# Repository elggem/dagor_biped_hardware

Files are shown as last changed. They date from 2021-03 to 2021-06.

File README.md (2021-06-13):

# dagor_biped_hardware

<p align="center">
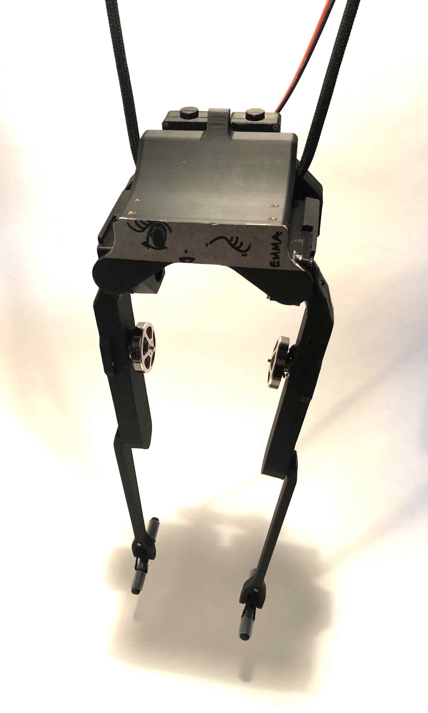
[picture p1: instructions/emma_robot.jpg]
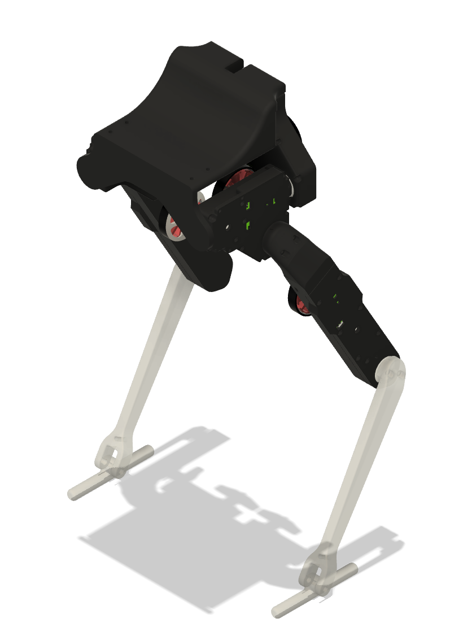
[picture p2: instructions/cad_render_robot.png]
    
</p>

This is a robot hardware design based on the the [Open Robot Dynamic Initiative](https://github.com/open-dynamic-robot-initiative/open_robot_actuator_hardware) Bolt robot remixed for easier and cheaper assembly using commonly available FDM 3D printers and control via the [Dagor Brushless motor control module](https://www.dagor.dev). The following modifications were made to the original design:

  - The body and cover of the actuator modules are modified to make them print easily without supports on an entry level FDM printer in ASA/PLA.
  - Change of belt to 3M HTD profile. This curved belt profile might not be ideal in terms of backlash and other performance characteristics, but it is more affordable than the AT3 GENIII Conti belts used in the original ODRI work. Other (trapezoidal) tooth profiles might be better suited for this application.
  - Change of gear ratio from 1:9 to 1:8. This leads to slightly less torque but also faster speed. The change was made to accomodate a bigger transmission pulley with 12/32 instead of 10/30 teeth, which allows printing the pulley on an FDM printer in PLA.
  - Change to 4004 360kV budget motors. Change to mounting holes and design of custom Hex-based motor pulley to avoid having to make a custom motor shaft.
  - Mounting holes for [Dagor Brushless Controller module](https://www.dagor.dev). 

## Instructions

### Motor pulley
<p align="center">
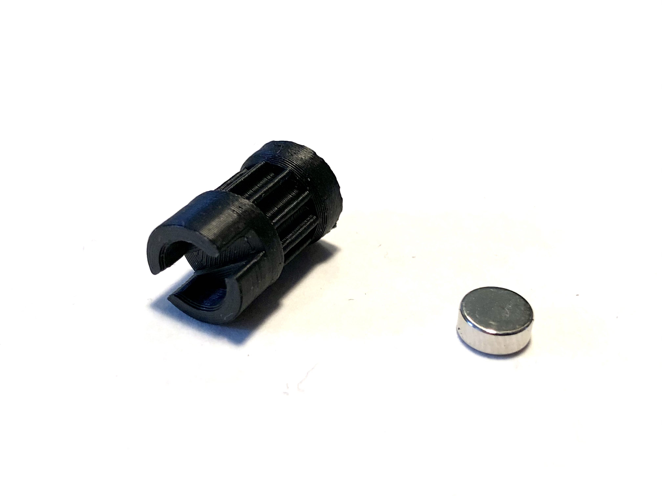
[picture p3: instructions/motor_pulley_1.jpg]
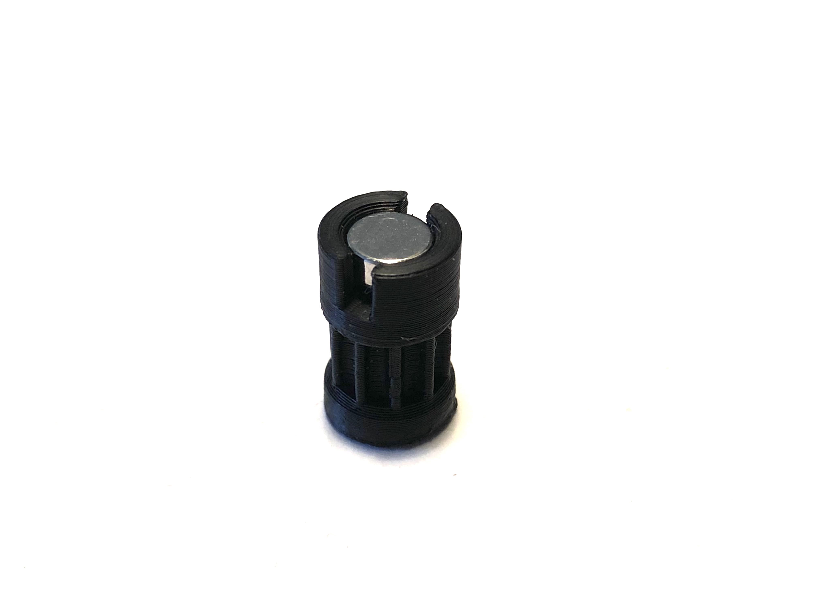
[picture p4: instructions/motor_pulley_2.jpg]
  
</p>

The motor pulley press-fits onto the brass or steel standoffs on the finished motor assembly. This pulley has to be printed using SLA with resin, it is too small to be printed using an FDM printer in my experience.

### Output pulley
<p align="center">
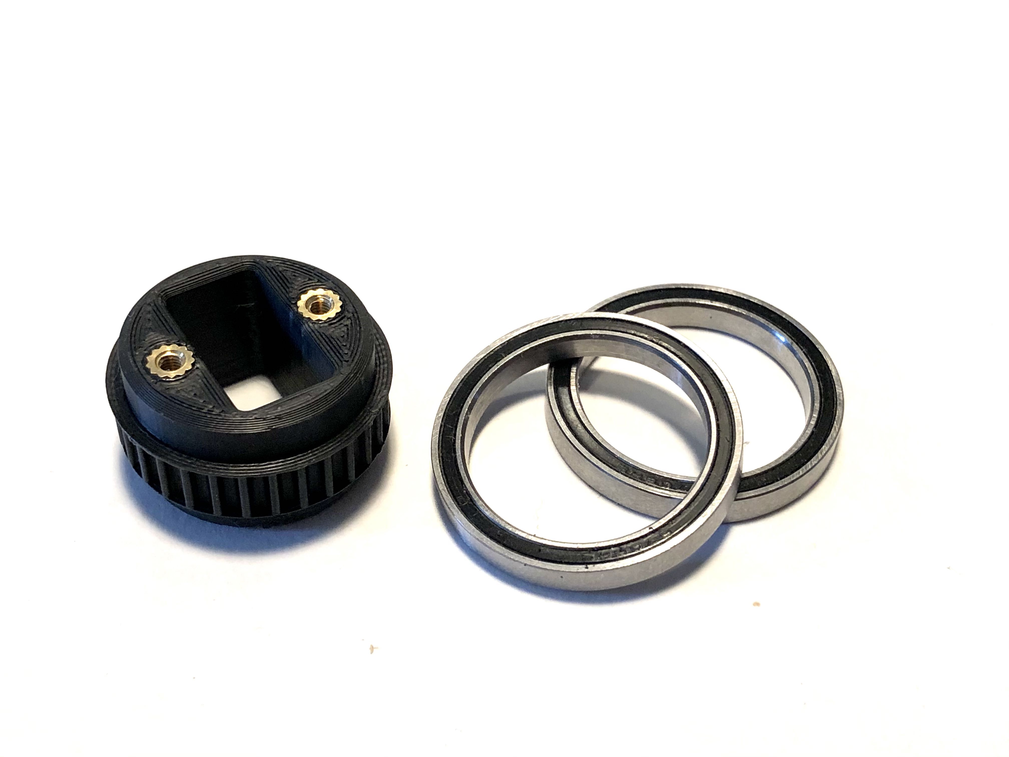
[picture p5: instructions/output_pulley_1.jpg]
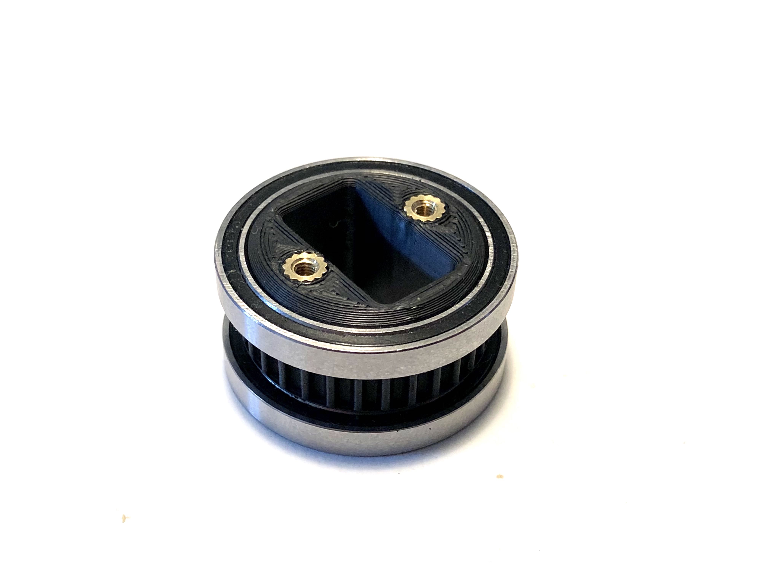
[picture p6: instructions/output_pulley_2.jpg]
  
</p>

Two threaded inserts are placed on the output pulley and two 6705 bearings attached.

### Center pulley

<p align="center">
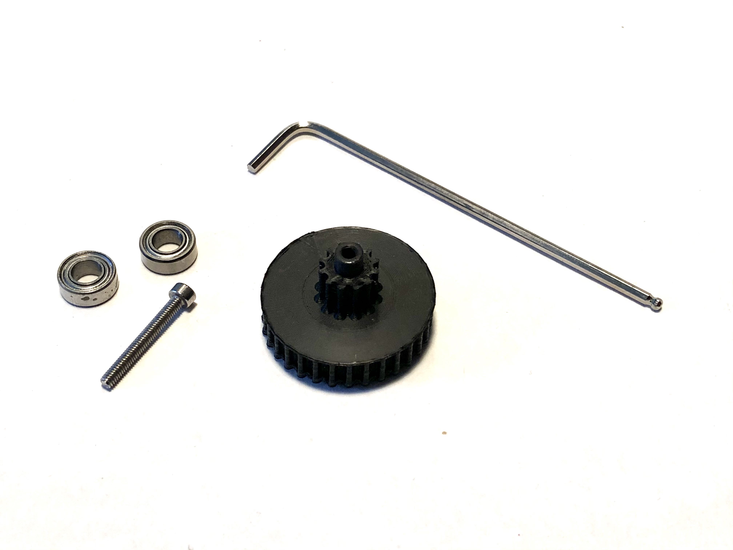
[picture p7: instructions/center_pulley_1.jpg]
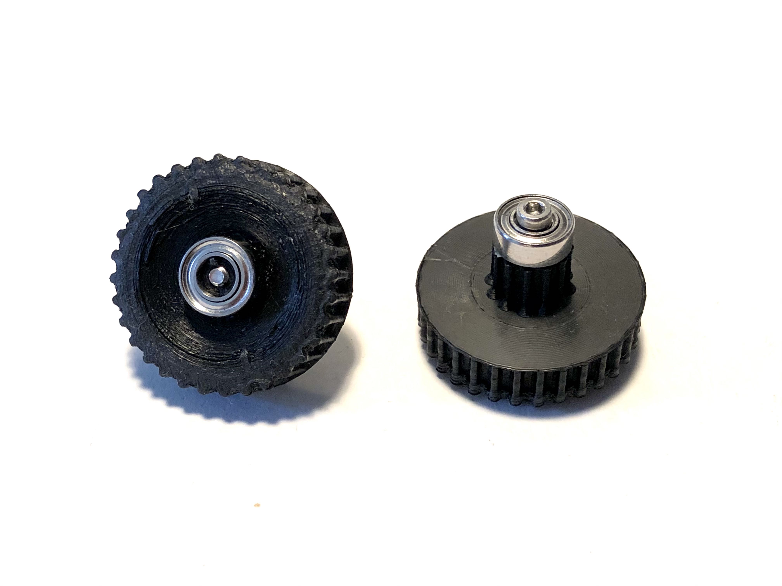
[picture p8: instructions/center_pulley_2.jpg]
  
</p>

The center transmission pulley is under a lot of stress and needs to be fabricated as strong as possible. In many other designs this pulley is machined from aluminium using CNC to avoid breaking it. It would also make sense to print it out of a strong material such as Nylon or Polycarbonate. To make this piece out of PLA, a few custom slicer settings need to be made for extra strength.

1. We printed the pulley with the maximum resolution of 0.08mm on an Ender 3 in PLA. This enables the underside of the pulley to print without supports.
2. Part cooling needs to be turned off during print except for the very top circular shape that connects to the bearing. In our case we turned on part cooling at layer 192. No part cooling increases layer adhesion significantly and is absolutely recommended. To make this work with enough precision we decreased the output perimeter speed to 5mm/s. 
3. The extrusion width needs to be optimized to avoid gaps between the tooth profile and inner body of the pulley. In our case the optimal extrusion width was 0.3mm for inner and outer perimeters.
4. We set the perimeter count to 32 so that the pulley prints entirely as perimeters with no infill. This maximizes the contact area between the bigger bottom pulley and smaller top pulley.
5. We set the extrusion multiplier to 105% to increase layer bonding even further.

After printing, a 20mm M2.5 bolt is screwed into the pulley to further strengthen it from top to bottom. Then the MR105 bearings can be press-fit into place.

### Preparing the motor shaft

<p align="center">
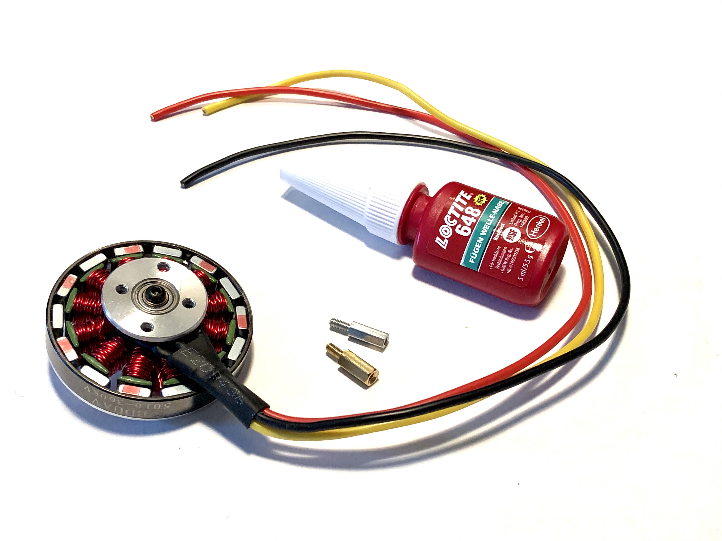
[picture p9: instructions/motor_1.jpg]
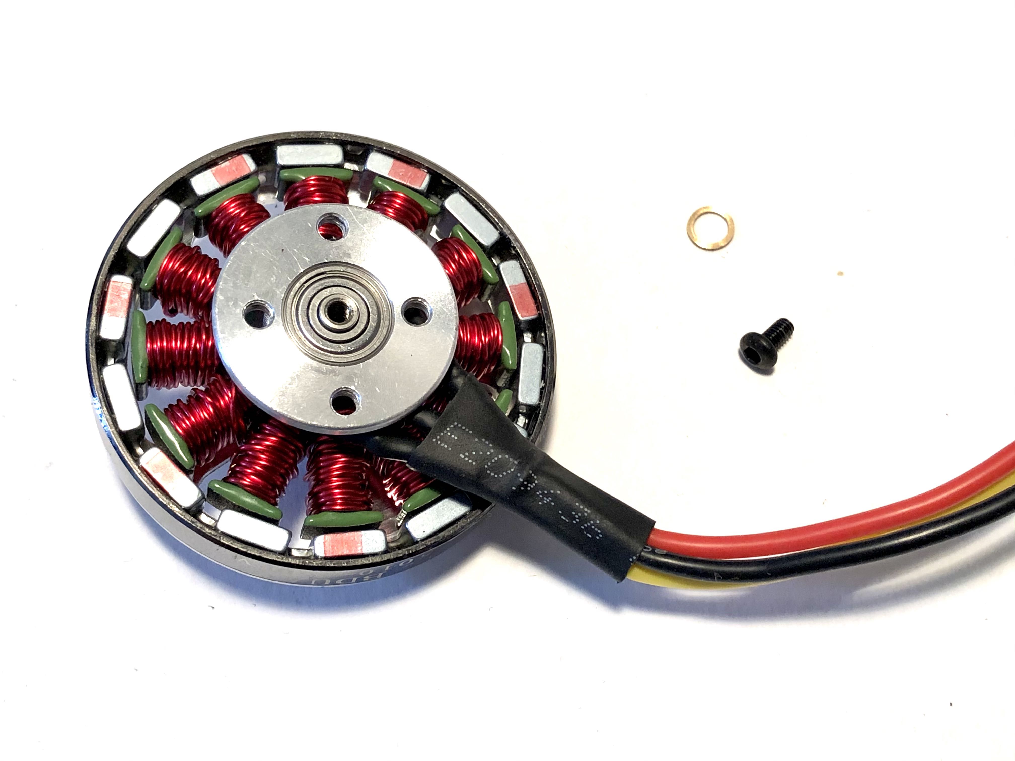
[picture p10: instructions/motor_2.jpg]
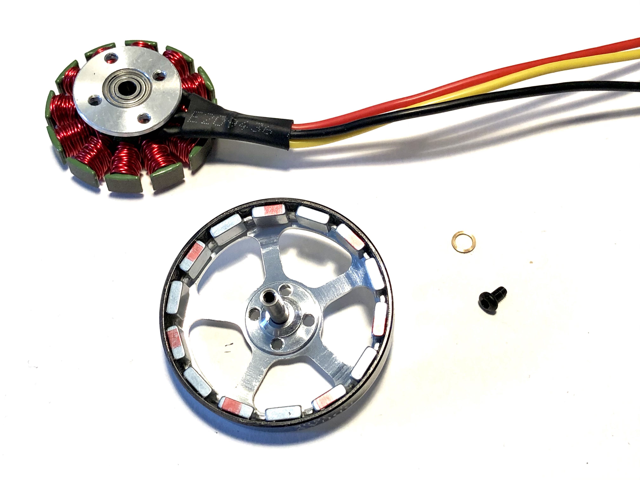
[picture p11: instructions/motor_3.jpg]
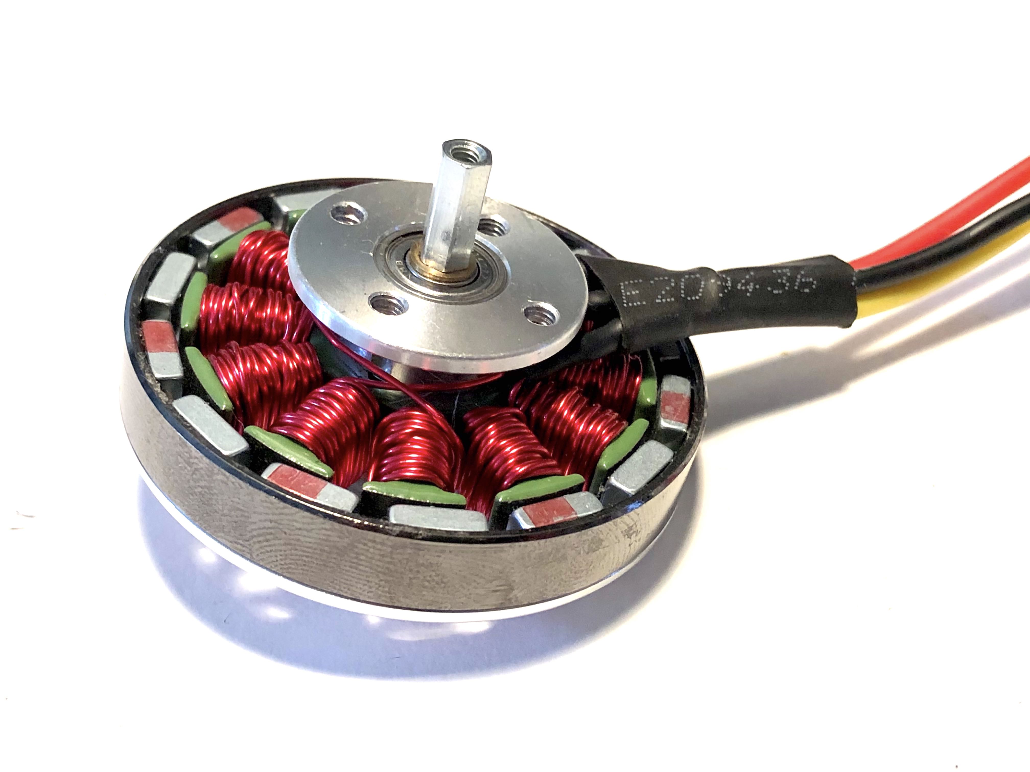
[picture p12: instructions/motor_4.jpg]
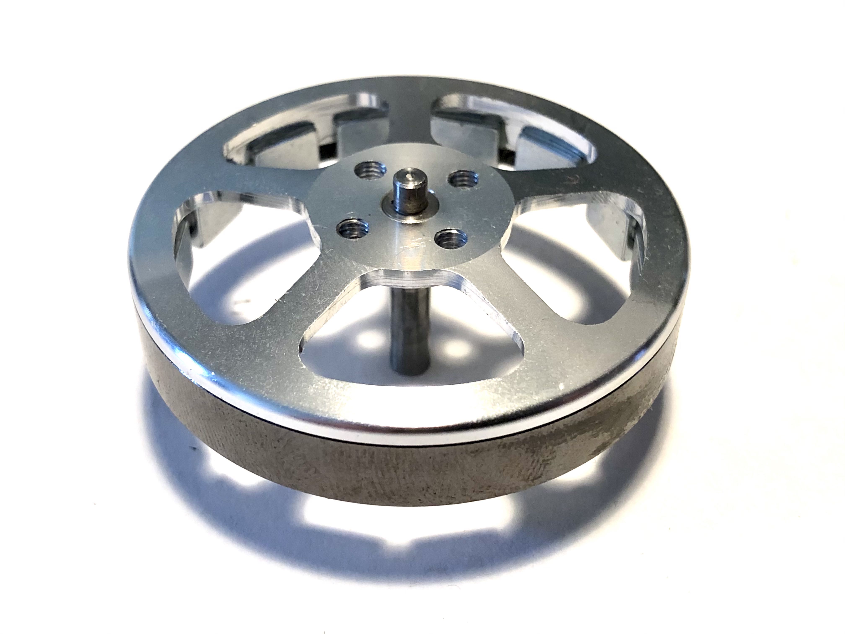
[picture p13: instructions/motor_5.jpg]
  
</p>

There are M2.5 threads on the output shaft of the Sunnysky motors we used in this build. If you use other motors or receive another batch of these motors without the thread then you have to find another way of mounting the output transmission pulley onto your motors. This might involve replacing the shaft of the motor entirely (for examples see [here](https://github.com/open-dynamic-robot-initiative/open_robot_actuator_hardware/blob/master/mechanics/actuator_module_v1/details/details_motor_shaft_preparation.md) and [here](https://youtu.be/HwWZw7wfN_k?t=182)). In our case, the process is quite simple:

 1. Remove the original M2.5 lockscrew on the output shaft of the motor and seperate the outer case from the stator. Due to the magnetic force this requires quite a bit of strength. Be aware not to pinch your fingers.
 2. Use a hard flat surface to push the output shaft from the outer case a little bit. Apply Loctite 648 or another suitable anaerobic metal glue onto the surfaces and push the shaft back into the housing. Remove any residual glue that was squeezed out from the outside.
 3. Snap the stator back into the housing carefully. After apply some Loctite 648 to the M2.5 standoff and screw it into the shaft as tight as possible with pliers. We use steel standoffs here, but the more commonly available brass standoffs would probably also work.
 4. Wait for the Loctite to cure at least 24hr. Then slide the 3D printed motor output pulley over the standoff. It should be a very tight press-fit between the pulley and standoff.
 5. Finally insert the magnet used for the magnetic encoder into place. It should also be a pretty tight fit. If it falls out very easily apply a little amount of glue to fix it in place.

### Preparing Dagor boards

<p align="center">
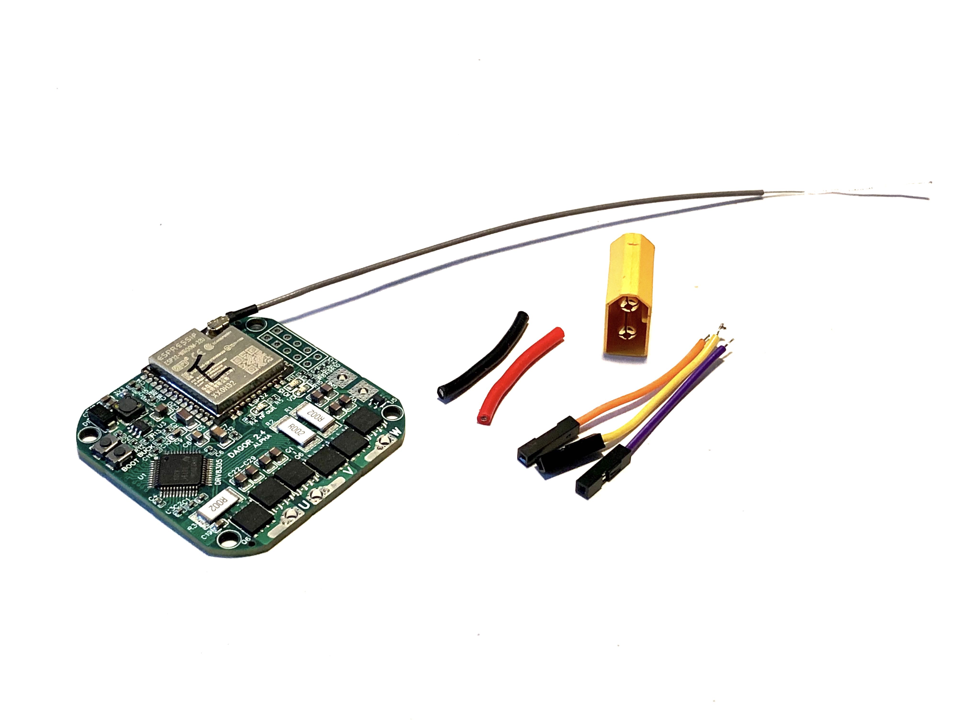
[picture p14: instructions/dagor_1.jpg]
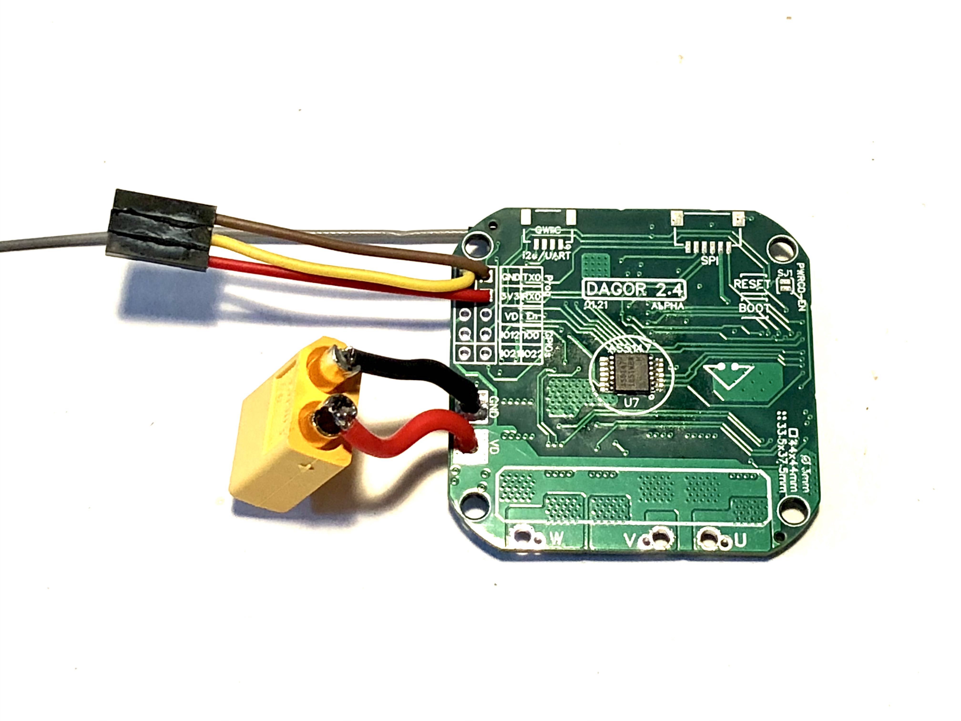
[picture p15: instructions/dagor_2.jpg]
  
</p>

 1. Prepare a 3-pin female programming header connection cable with ~4cm length and put some solder on the exposed leads. Solder the programming wires on to RXD/TXD/GND on the Dagor board, with the leads exiting the PCB towards the side with the magnetic encoder. 
 2.  Prepare an XT60 male connector with ~2cm leads for the hip modules and a ~15cm power wire without a connector for the leg modules. Solder the power wires on the side of the module with the magnetic encoder.
 3. Optionally you could use bullet style connectors for the motor wires, but I choose to solder them onto the board directly after assembly. If you want to also solder directly just put some tin onto the pads of the controller. The leg modules have enough space for connectors but in the hip modules its a very tight fit.

### Actuator assembly

<p align="center">
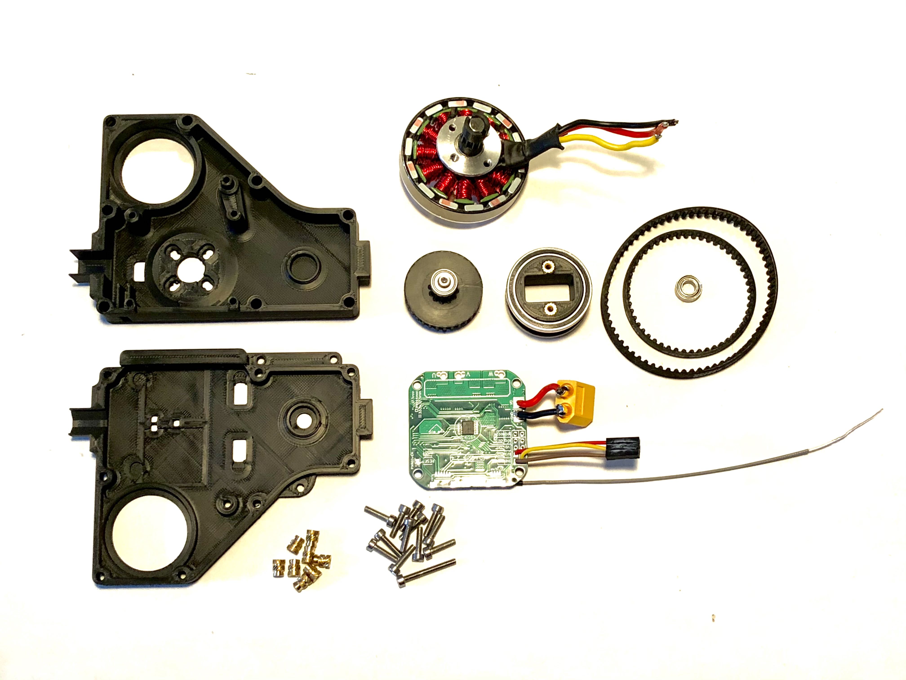
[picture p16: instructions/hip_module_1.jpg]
  
</p>
<p align="center">
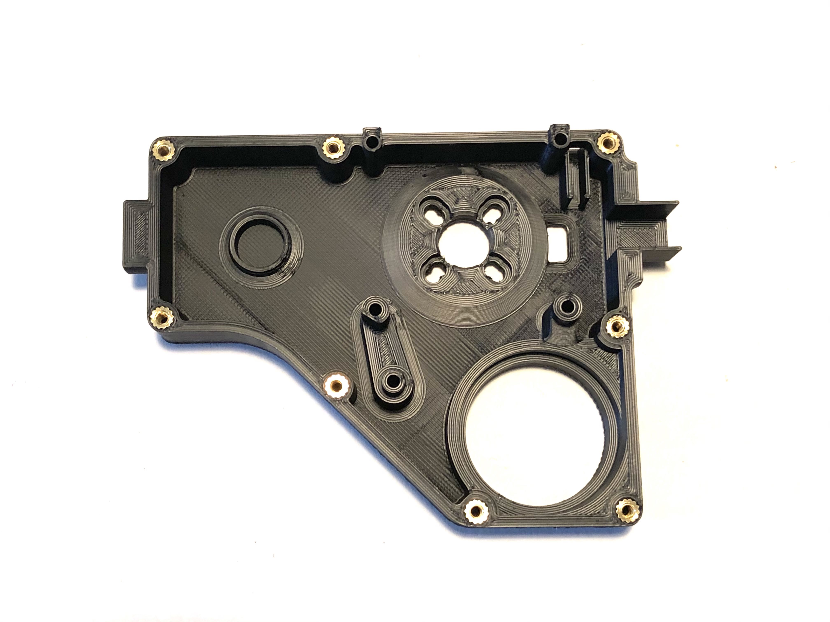
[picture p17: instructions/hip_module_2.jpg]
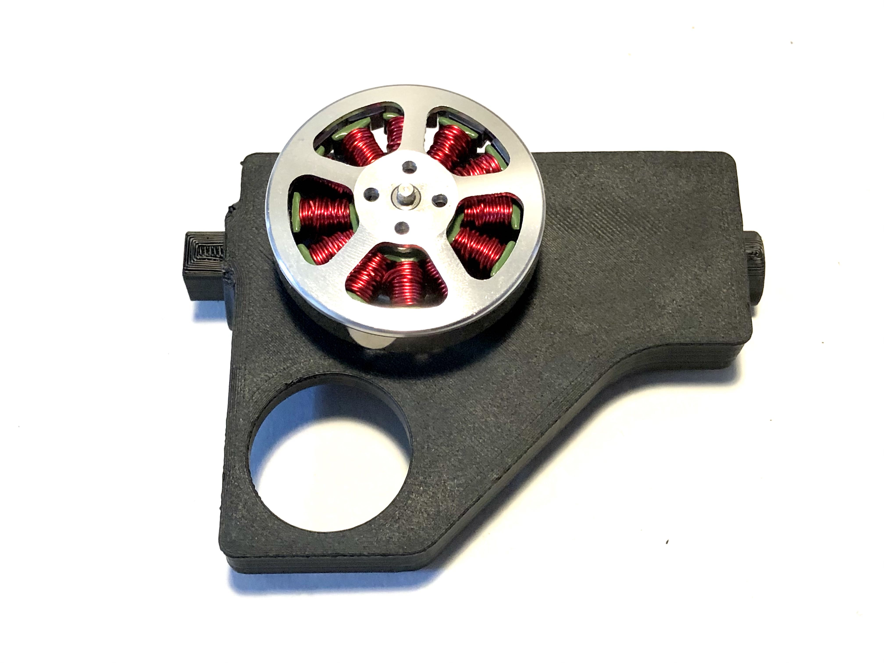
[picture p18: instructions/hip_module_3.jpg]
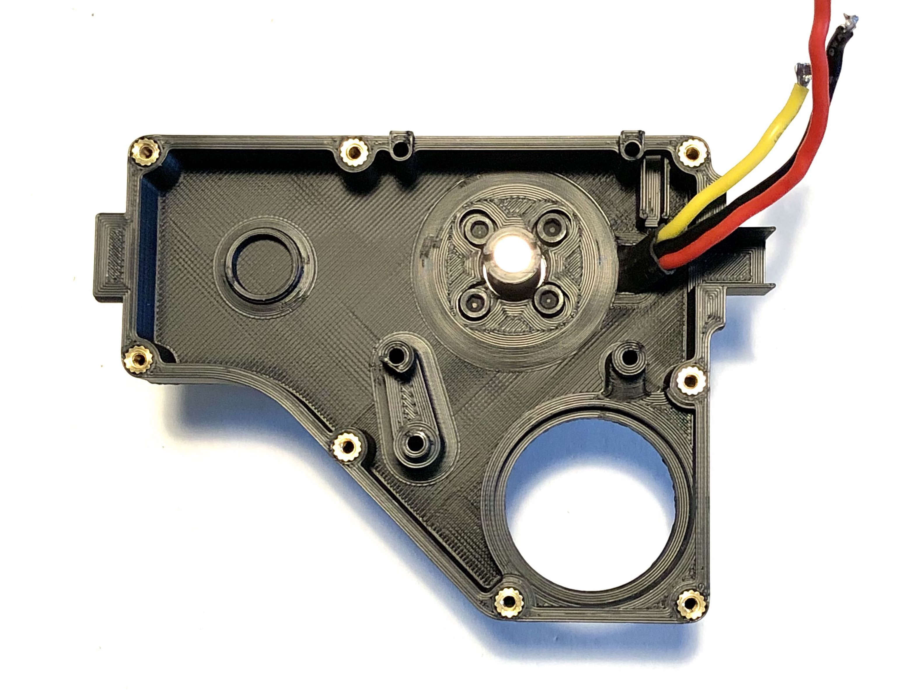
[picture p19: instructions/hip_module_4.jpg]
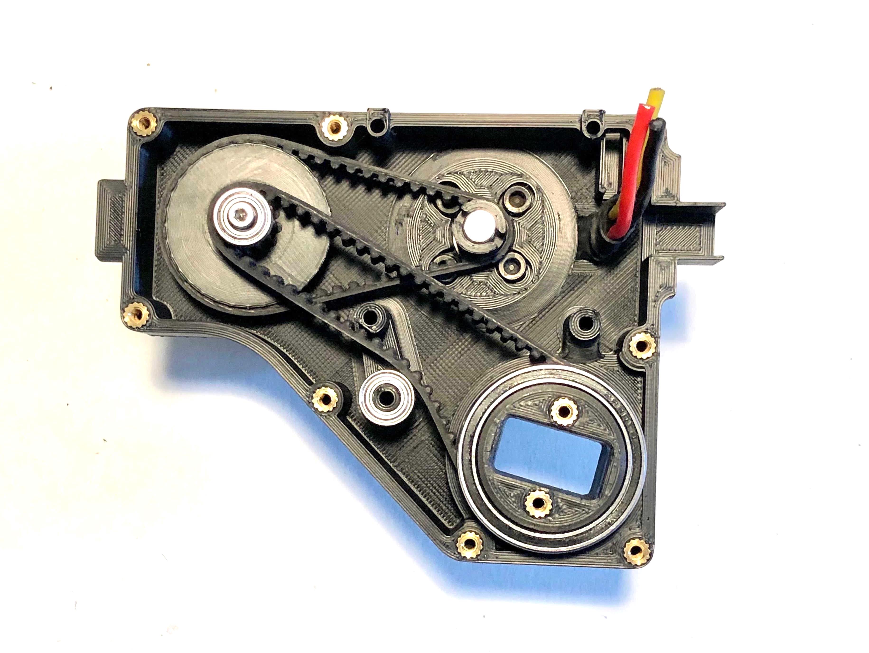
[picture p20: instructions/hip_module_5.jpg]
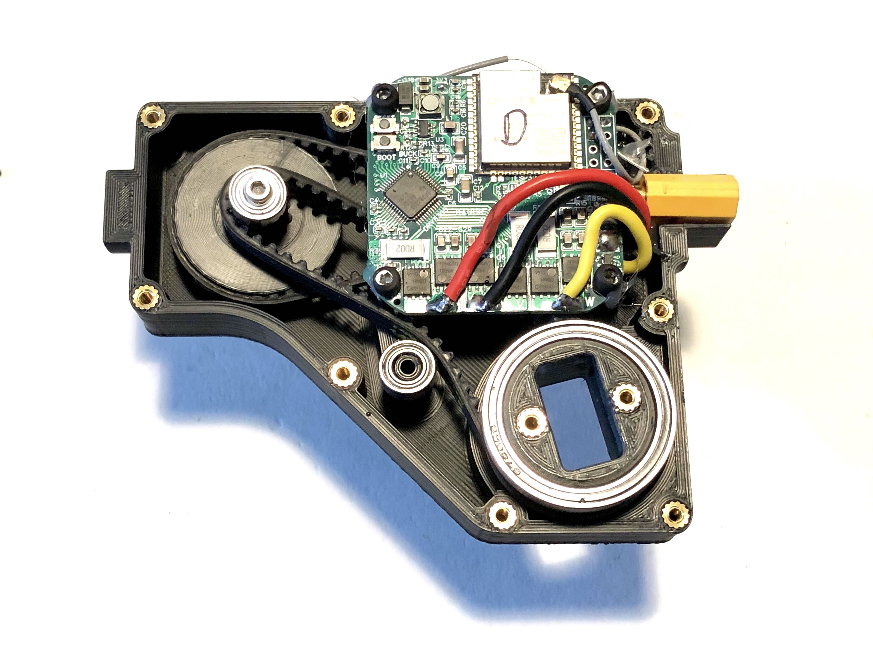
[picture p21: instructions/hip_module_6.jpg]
  
</p>

*Final weight of hip module: 188g*

Make sure that both the smaller MR105 and bigger 6705 bearings press fit tightly in their places!

1. Use a soldering iron to place 8x threaded inserts into the provided holes on the body of the actuator module.
2. Mount the finished motor assembly onto the body of the actuator module, feeding the wires through the hole. Dont worry about the length of the motor cables at this point.
3. Take the assembled transmission pulley and press it into the mounting hole while adding the 50 tooth belt between the motor and transmission pulleys. There will be some tension here and the transmission pulley will be slightly slanted towards the motor. That is ok. You can keep tension on the transmission pulley and give the motor a few turns to see if it is spinning freely.
4. Press fit an MR105 bearing onto the belt tensioning post in the body of the module. Make sure it sits flush with the bottom and be sure not to apply too much force to the post. It will be strengthened by a bolt in the final stage of assembly.
5. Place the output pulley assembly into its hole on the body while adding the 67 tooth belt between it and the transmission pulley. Quickly give the motor a few turns while keeping pressure on the transmission pulley to make sure the output pulley turns. Dont apply too much force to avoid breaking the belt tensioning post.
7. Place a Dagor board onto the mounting posts and screw in 4x M2.5 bolts to secure it.
8. Place the programming and power connectors into their sockets and glue them into place with either hotglue or superglue.
9. Shorten and solder the motor wires onto the Dagor board. Optionally you can use bullet style connectors for this.
10. Place the cover on top of the base. You need to slip it over one side of the Dagor board and wiggle both the transmission and output pulleys into place to make it work. The belt tension will make this a bit tricky, be patient and dont apply too much force.
11. Screw the 8x M2.5 10mm bolts into place securing everything.
12. Finally, screw one M2.5 20mm bolt into the hole of the belt tensioner. This is essential because otherwise the belt tensioning post will break off.
13. Check that everything runs smoothly by giving the motor a few turns and backdriving the actuator from the output shaft. After, flash the firmware on Dagor and begin testing.

## Bill of Materials

This is a preliminary list subject to change.

### 3D printed parts

| Name 							  | qty |
| --- | --- |
| hip_normal_body					| 2 |
| hip_normal_cover					| 2 |
| hip_mirrored_body					| 2 |
| hip_mirrored_cover				| 2 |
| upper_leg_structure_base			| 2 |
| upper_leg_structure_cover			| 2 |
| upper_leg_structure_output_shaft	| 2 |
| lower_leg_structure				| 2 |
| foot_structure					| 2 |
| body_structure					| 1 |
| motor_pulley						| 6 |
| transmission_pulley				| 6 |
| output_pulley						| 6 |

### Mechanical components

| Name 							| qty  |
| --- | --- |
| Belt 3M HTD 150mm/50t/4mm 	| 3 |
| Belt 3M HTD 201mm/67t/6mm		| 3 |
| Bearing 6705 25x32x4			| 12 |
| Bearing MR105 5x10x4			| 18 |
| M2.5 threaded inserts			| 48 |
| M2.5 x 10mm screw				| 48 |
| M2.5 x 20mm screw				| 16 |
| M2.5 distance bolt 10mm		| 6 |
| Motor encoder magnet 		| 6 |

### Electrical components

| Name 							| qty  |
| --- | --- |
| Dagor board 					| 6 |
| u.fl IPEX antenna  			| 6 |
| Sunnysky 5010 360kV motor		| 6 |
| XT60 male connector			| 6 |

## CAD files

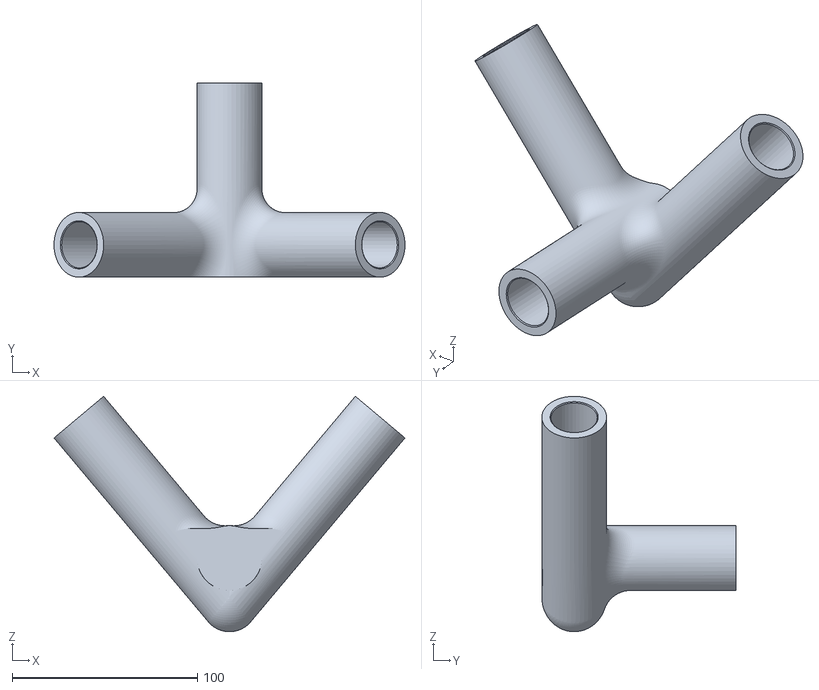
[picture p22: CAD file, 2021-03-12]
mechanics/biped_stand_v1/stl_files/mainstand.stl
189.5 x 105.0 x 127.1

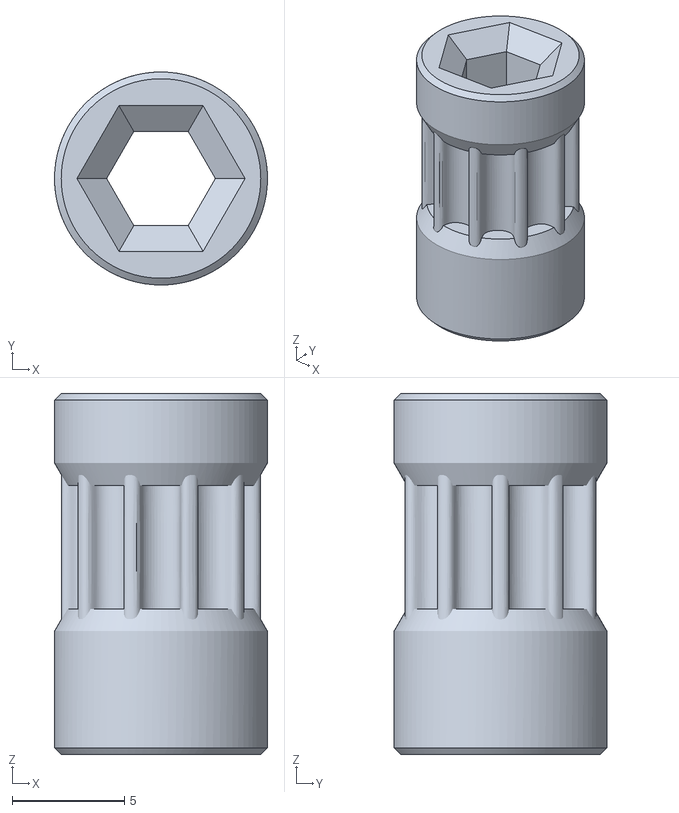
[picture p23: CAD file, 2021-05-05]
mechanics/actuator_module_v1/stl_files/transmission_pulley_htd_t10_motor_steel_standoff.stl
9.50 x 9.50 x 16.1

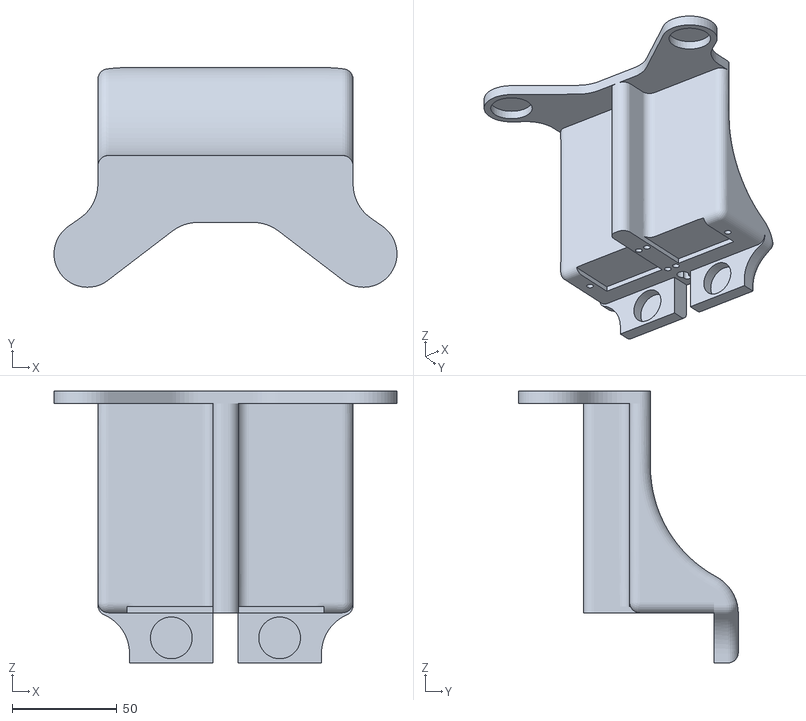
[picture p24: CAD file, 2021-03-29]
mechanics/biped_6dof_v1/stl_files/_body_structure.stl
164.0 x 105.0 x 130.0

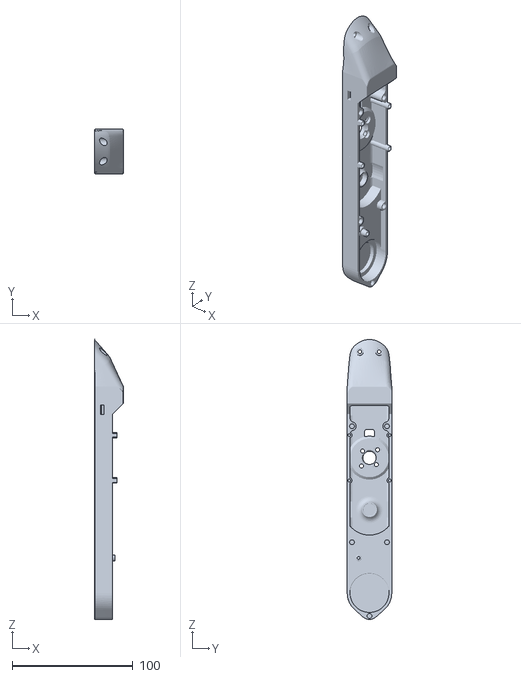
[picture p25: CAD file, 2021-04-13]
mechanics/biped_leg_3dof_v1/stl_files/upper_leg_200mm_body.stl
24.0 x 37.0 x 232.1

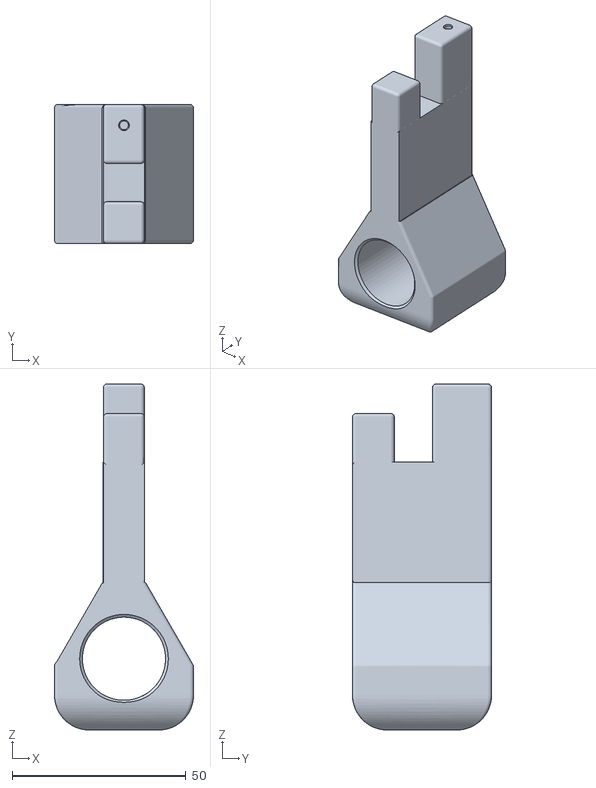
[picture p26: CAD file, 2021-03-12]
mechanics/biped_stand_v1/stl_files/attachment.stl
40.0 x 40.0 x 99.5

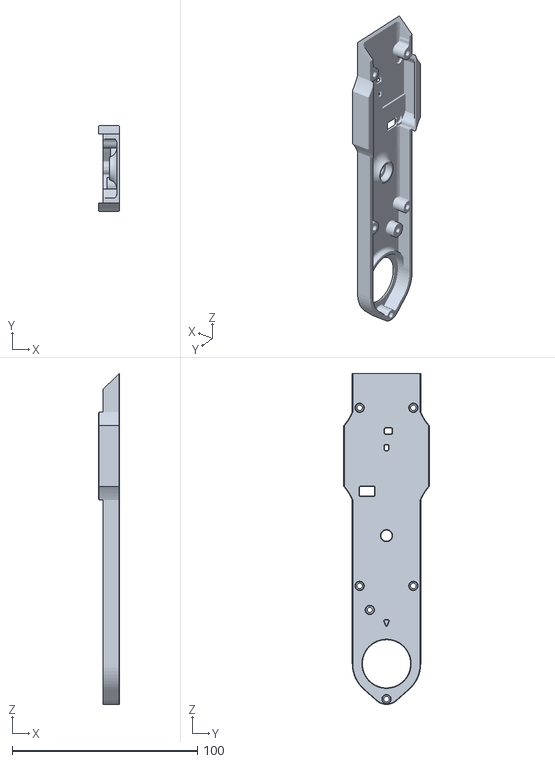
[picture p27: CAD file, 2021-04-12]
mechanics/biped_leg_3dof_v1/stl_files/upper_leg_200mm_cover.stl
11.5 x 46.2 x 178.6

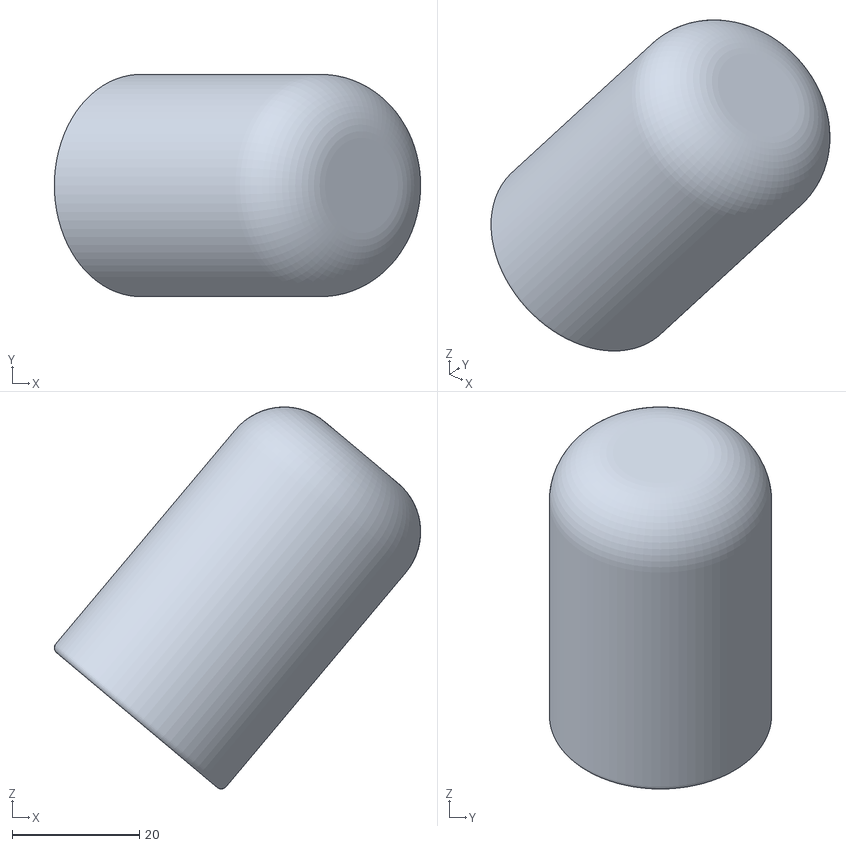
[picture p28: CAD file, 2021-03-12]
mechanics/biped_stand_v1/stl_files/foot.stl
57.7 x 35.0 x 60.1

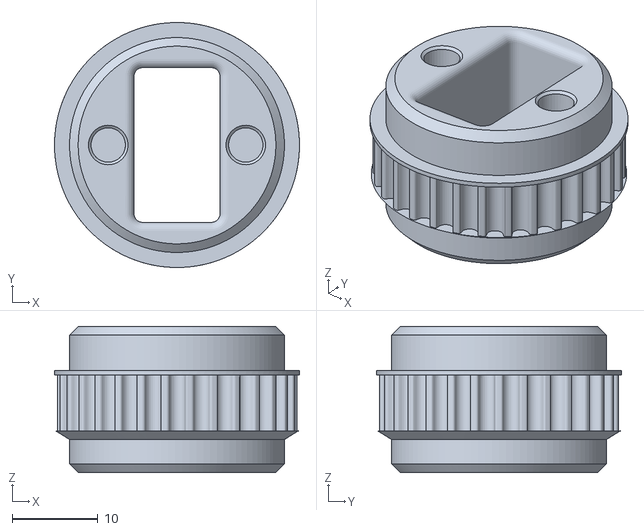
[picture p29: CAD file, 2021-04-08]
mechanics/actuator_module_v1/stl_files/transmission_pulley_htd_t30_output.stl
28.5 x 28.5 x 17.0

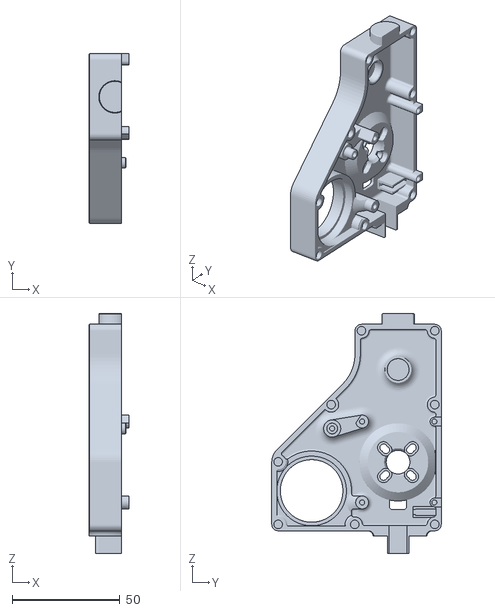
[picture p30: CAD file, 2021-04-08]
mechanics/biped_leg_3dof_v1/stl_files/hip_normal_body.stl
18.5 x 78.6 x 111.2

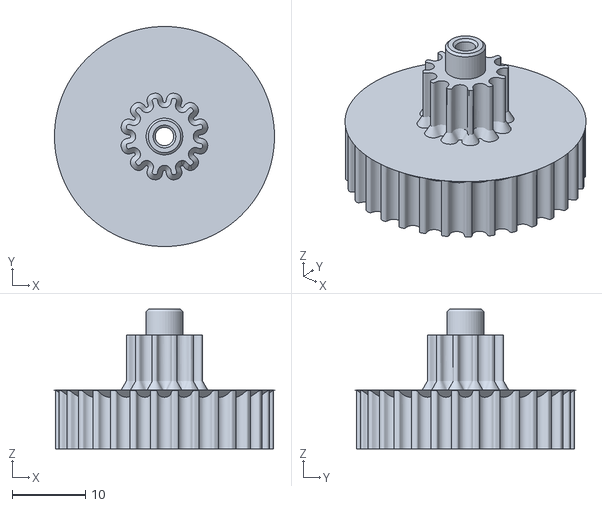
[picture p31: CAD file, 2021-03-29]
mechanics/actuator_module_v1/stl_files/transmission_pulley_htd_t12_center.stl
29.9 x 29.9 x 19.0

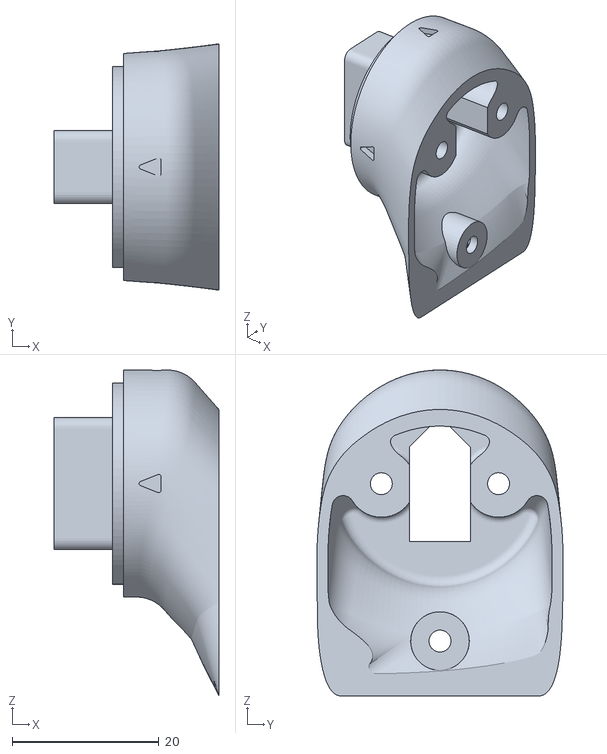
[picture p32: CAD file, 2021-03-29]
mechanics/biped_leg_3dof_v1/stl_files/upper_leg_200mm_output_shaft.stl
22.5 x 33.6 x 44.5

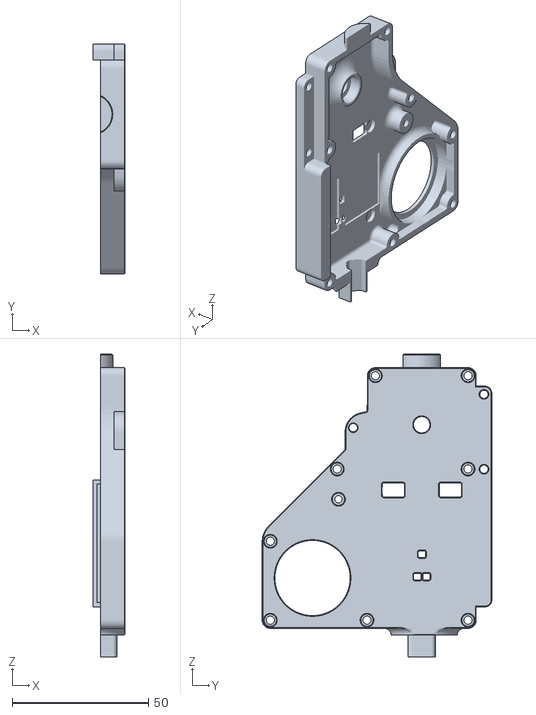
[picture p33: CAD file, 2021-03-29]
mechanics/biped_leg_3dof_v1/stl_files/hip_normal_cover.stl
11.8 x 84.3 x 111.2

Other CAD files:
mechanics/actuator_module_v1/cad_files/transmission_pulley_htd_t10_motor_steel_standoff.f3d
mechanics/actuator_module_v1/cad_files/transmission_pulley_htd_t12_center.f3d
mechanics/actuator_module_v1/cad_files/transmission_pulley_htd_t30_output.f3d
mechanics/biped_6dof_v1/cad_files/_body_structure.f3d
mechanics/biped_leg_3dof_v1/cad_files/_hip_normal.f3z
mechanics/biped_leg_3dof_v1/cad_files/_upper_leg_200mm.f3z

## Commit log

2021-02-15 initial commit original designs
    [body_structure_biped_back.STL, body_structure_biped_bottom.STL, body_structure_biped_front.STL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]
2021-02-15 removing some non-final assemblies
    [body_structure_biped_back.STL, body_structure_biped_bottom.STL, body_structure_biped_front.STL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]
2021-02-19 update readme with print instructions
2021-02-23 first beta designs
    [foot_structure.STL, lower_leg_structure_200mm.STL, transmission_pulley_at3_t30_center.stl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]
2021-02-24 updated pulleys
    [transmission_pulley_htd_t10_center.stl, transmission_pulley_htd_t10_motor.stl, transmission_pulley_htd_t30_output.stl]
2021-02-24 update motor pulley
    [transmission_pulley_htd_t10_motor.stl]
2021-02-26 new pulleys and body for threaded inserts
    [transmission_pulley_htd_t10_center.stl, upper_leg_200mm_body.stl, upper_leg_200mm_cover.stl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]
2021-02-26 belt tensioners for both belts, moving motor tensioners 0.75mm closer to centerpoint
    [upper_leg_200mm_body.stl, upper_leg_200mm_cover.stl]
2021-02-27 adding top structure stls
    [body_structure_biped_back.stl, body_structure_biped_bottom.stl, body_structure_biped_front.stl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]
2021-02-27 fixing back structure holes
    [body_structure_biped_back.stl]
2021-02-28 update front structure fitting for bearings
    [body_structure_biped_front.stl]
2021-03-07 adding preliminary hip modules left side
    [hip_aa_left_body.stl, hip_aa_left_cover.stl, hip_fe_left_body.stl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]
2021-03-07 new pulleys
    [transmission_pulley_htd_t10_center.stl, transmission_pulley_htd_t10_motor.stl]
2021-03-07 adding right hip modules
    [hip_aa_right_body.stl, hip_aa_right_cover.stl, hip_fe_left_body.stl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]
2021-03-07 updated body structure for clearance to motors
    [body_structure_biped_back.stl, body_structure_biped_front.stl, body_structure_biped_left_side.stl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]
2021-03-09 new fe hip modules with updated clearance
    [hip_fe_left_body.stl, hip_fe_left_cover.stl, hip_fe_right_body.stl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]
2021-03-12 adding stand stl files
    [attachment.stl, foot.stl, mainstand.stl]
2021-03-17 update pulleys
    [transmission_pulley_htd_t10_motor.stl, transmission_pulley_htd_t10_motor_highwidth.stl, transmission_pulley_htd_t10_motor_thinwidth.stl]
2021-03-17 new unibody upper leg design
    [upper_leg_200mm_body.stl, upper_leg_200mm_cover.stl, upper_leg_200mm_output_shaft.stl]
2021-03-17 update clearances on motor pulley
    [transmission_pulley_htd_t10_motor.stl]
2021-03-18 body structure simplification
    [_body_structure.stl, body_structure_biped_back.stl, body_structure_biped_bottom.stl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]
2021-03-18 hip module simplification and unibody design
    [hip_aa_left_body.stl, hip_aa_left_cover.stl, hip_aa_right_body.stl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]
2021-03-19 hip body revision, make pcb holder standoff smaller, increase programming header clearance
    [hip_normal_body.stl]
2021-03-29 updated transmission pulley
    [transmission_pulley_htd_t10_center.stl, transmission_pulley_htd_t10_center_composite_bottom.stl, transmission_pulley_htd_t10_center_composite_top_cutout.stl]
2021-03-29 update body structure and actuator modules
    [_body_structure.stl, hip_normal_body.stl, hip_normal_cover.stl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]
2021-03-29 rename output transmission pulley for brass standoffs
    [transmission_pulley_htd_t10_motor_brass_standoff.stl]
2021-03-29 adding steel standoff motor pulley
    [transmission_pulley_htd_t10_motor_steel_standoff.stl]
2021-04-08 final hip and leg modules, update to transmission pulley
    [hip_normal_body.stl, transmission_pulley_htd_t10_motor_steel_standoff.stl, transmission_pulley_htd_t30_output.stl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]
2021-04-10 remove fillet from body to avoid ASA warping
    [upper_leg_200mm_body.stl]
2021-04-10 rename center pulley
    [transmission_pulley_htd_t12_center.stl]
2021-04-10 adding fusion 360 CAD files
    [_body_structure.f3d, _hip_normal.f3z, _upper_leg_200mm.f3z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]
2021-04-12 remove middle fasteners for leg module to avoid bumping into belt
    [upper_leg_200mm_body.stl, upper_leg_200mm_cover.stl]
2021-04-13 cutout for transmission pulley in leg
    [upper_leg_200mm_body.stl]
